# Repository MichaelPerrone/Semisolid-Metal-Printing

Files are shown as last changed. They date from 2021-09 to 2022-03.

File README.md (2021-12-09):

# Semisolid-Metal-Printing
Extrusion system for printing metal on RepRap 3D printers.

This repository contains 3D models, firmware and software configurations for installing a semisolid metal extruder on the venerable old Prusa Mendel i2 because it is a reasonably good prototyping platform. 

Eventually it will contain the same for other common RepRaps that are more popular nowadays, perhaps to be used to make pull requests for those other projects.

See the instructions on my Hackaday page:
https://hackaday.io/project/179846-semisolid-metal-printing
they are reasonably good at this point.

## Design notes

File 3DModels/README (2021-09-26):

V1 was an attempt at using MHD extrusion of liquid metal; perhaps the parts and methods used will help someone else with their project, but it didn't end up being useful for this one. Will elaborate on that system later.
V2 is the current working system. It uses a liquid gasket to enable filament extrusion of metal in just the same way as plastic.
V2 is meant to reuse some of the parts from V1, for hooking up the system to a Prusa Mendel printer. Systems for attaching to more modern printers will come after the concept has been proven out.

The V2 parts are compatible with the parts from V1 for hooking this system up to a Prusa Mendel printer and a Bondtech extruder, The spacer with all the hexagonal cuts is meant to be laser cut out of wood.
In Lieu of instructions for now, a picture of the Onshape assembly will suffice for assembly. More detailed instructions on the way.

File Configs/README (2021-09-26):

Firmware and software configs for Marlin and other 3D printing firmwares will go here.
Recommended print settings for path planning will also go here.

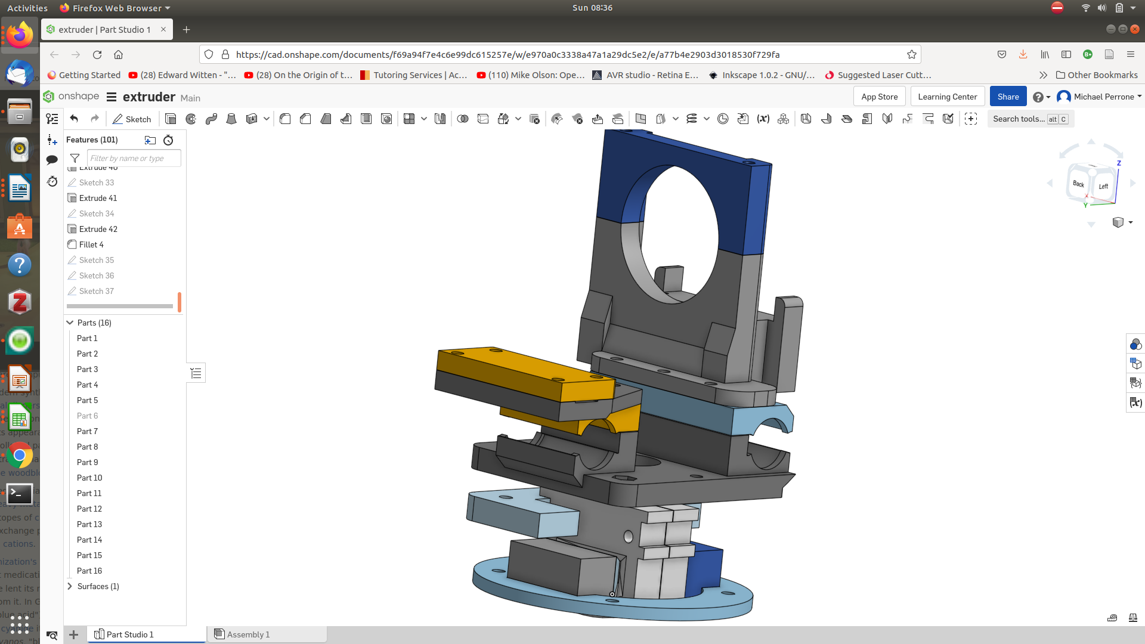
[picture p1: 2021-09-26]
3DModels/V1PrusaMendel/Screenshot from 2021-09-26 08-36-41.png

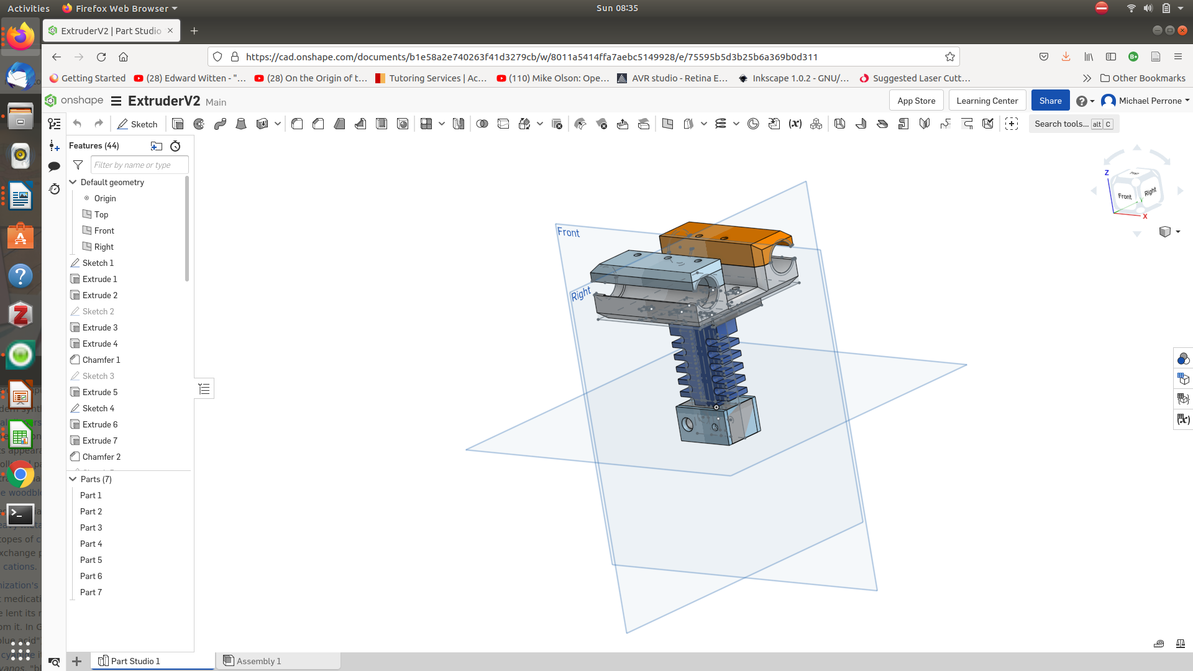
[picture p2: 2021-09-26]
3DModels/V2PrusaMendel/Screenshot from 2021-09-26 08-35-54.png

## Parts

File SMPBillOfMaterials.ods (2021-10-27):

For the extruder retrofit specifically
Item | Price | Quantity | Total | Link | Notes
M3 bolts | 11.33 | 1 | 11.33 | https://www.mcmaster.com/91290A124/
M3 bolts | 13.05 | 1 | 13.05 | https://www.mcmaster.com/91290A119/
M3 nuts | 1.17 | 1 | 1.17 | https://www.mcmaster.com/90592A085/
Mild steel bar | 9.77 | 1 | 9.77 | https://www.mcmaster.com/8910K758-9143K521/
Aluminum 6061 bar | 7.61 | 1 | 7.61 | https://www.mcmaster.com/8975K43-9140T124/ | Can cut sections of this to make thermal breaks
M6 Threaded rod | 7.5 | 1 | 7.5 | https://www.mcmaster.com/93325A418/
X-Pando | 16.91 | 1 | 16.91 | https://www.mcmaster.com/6818K11/
E3D-sized 60W heater cartridge | 8.45 | 1 | 8.45 | https://www.amazon.com/24V-60W-Temperature-Cartridge-Extruder/dp/B08CNCHC29?qsid=132-1475246-8798325
E3D Thermistor cartridge | 9.48 | 1 | 9.48 | https://www.amazon.com/Genuine-E3D-Thermistor-Cartridge-E-SEMITEC-50-MOLEX/dp/B072HNL9MR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
PETG | 21.99 | 1 | 21.99 | https://www.amazon.com/OVERTURE-Filament-Consumables-Dimensional-Accuracy/dp/B07PDV9RC8
M3 Bolts | 11.71 | 1 | 11.71 | https://www.mcmaster.com/91290A135/ | 35mm long
 |  |  | 0
 |  |  | 0
 |  |  | 0
 |  |  | 118.97 |  | Many of the components are sold in large quantities: cost can be reduced if done as a group order
For the high temperature heat bed
Item | Price | Quantity | Total | Link | Notes
Aluminum plate | 19.69 | 1 | 19.69 | https://www.mcmaster.com/9246K11/
SmCo Magnets | 4.55 | 6 | 27.3 | https://www.mcmaster.com/5716K73/
Spring Steel Sheet | 25.66 | 1 | 25.66 | https://www.mcmaster.com/9071K74/
Silicone Washers | 10.97 | 1 | 10.97 | https://www.mcmaster.com/1182N006/
High Temperature Heat Bed | 109.99 | 1 | 109.99 | https://www.filastruder.com/products/e3d-high-temperature-heated-beds
Thermal paste | 6.9 | 1 | 6.9 | https://www.amazon.com/Arctic-Silver-AS5-3-5G-Thermal-Paste/dp/B0087X728K?qsid=132-1475246-8798325
Plywood |  |  | 0 |  | tbd
M3 screws |  |  | 0 |  | tbd
m3 nuts |  |  | 0 |  | tbd
 |  |  | 0
 |  |  | 0
 |  |  | 0
 |  |  | 0
 |  |  | 0
 |  |  | 200.51 |  | Might not be 100% required to get semisolid metal printing capability, but does make it way easier
Consumables
Item | Price | Quantity | Total | Link | Notes
Borax | 13.99 | 1 | 13.99 | https://www.amazon.com/Pure-Organic-Ingredients-Multipurpose-Ingredient/dp/B01N6LF59Y
Boric acid | 6.9 | 1 | 6.9 | https://www.amazon.com/Boric-Granular-Powder-Create-solution/dp/B014JJ9846?qsid=132-1475246-8798325 | Good to stock up on borax or boric acid for when they figure out P-B11 fusion
Glycerol | 6.99 | 1 | 6.99 | https://www.amazon.com/Glycerin-Supplier-Vegetable-USP-250ml/dp/B0762179GF?qsid=132-1475246-8798325
Pentaerythritol59.99 | 59.99 | 1 | 59.99 | https://www.amazon.com/EASTCHEM-Pentaerythritol-1pound-MF-115-77-5/dp/B07QYZP89H?qsid=132-1475246-8798325
Zinc | 13.89 | 1 | 13.89 | https://www.rotometals.com/zinc-ingot-99-8-full-ingot/
Tin | 28.99 | 1 | 28.99 | https://www.rotometals.com/tin-ingot-99-9-pure/
sodium hydroxide | 13.09 | 1 | 13.09 | https://www.amazon.com/Lab-Grade-Sodium-Hydroxide-Pellet-100g/dp/B077T7K9V2
sodium or potassium nitrate | 19.95 | 1 | 19.95 | https://www.amazon.com/Potassium-Nitrate-Purity-Milled-Reagent/dp/B094JZSN51?qsid=132-1475246-8798325
sulfuric acid | 17.99 | 1 | 17.99 | https://www.amazon.com/Sulfuric-Acid-Solution-1-0M-500mL/dp/B07JBNJL3L
trisodium phosphate | 15.95 | 1 | 15.95 | https://www.amazon.com/Trisodium-Phosphate-Heavy-duty-Degreaser/dp/B098PGM45Y | Mainly for degreasing
 |  |  | 0
 |  |  | 0
 |  |  | 0
 |  |  | 0
 |  |  | 197.73 |  | Only small amounts of these are needed: can split the cost in a group order
Equipment | (For making your own filament) |  | Notes | $
Wire drawing die |  | https://www.amazon.com/NEWTRY-0-26-4-0mm-Stainless-Drawplate-Tungsten/dp/B079BGBG1H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 |  | ~50
Wire rolling mill |  | https://www.amazon.com/Jewelry-Rolling-Machine-Combination-Flatten/dp/B09HC2FTHY |  | ~250
Melting furnace |  | https://www.amazon.com/TOAUTO-Upgraded-Electric-Refining-Precious/dp/B088B8PZVK?qsid=132-1475246-8798325 | Comes with tongs and equipment | ~350
Strip casting mold |  | https://www.amazon.com/Ingot-Combination-Cavity-Wires-Double/dp/B08DDF5M55?qsid=132-1475246-8798325 |  | ~50 | These aren’t the only equipment options to do this with

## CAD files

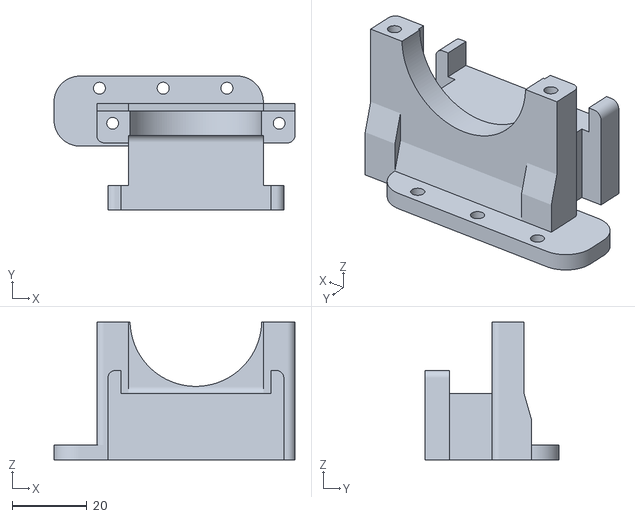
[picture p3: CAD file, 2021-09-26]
3DModels/V1PrusaMendel/Part Studio 1 - Part 10 - V1V2.stl
64.7 x 35.9 x 37.0

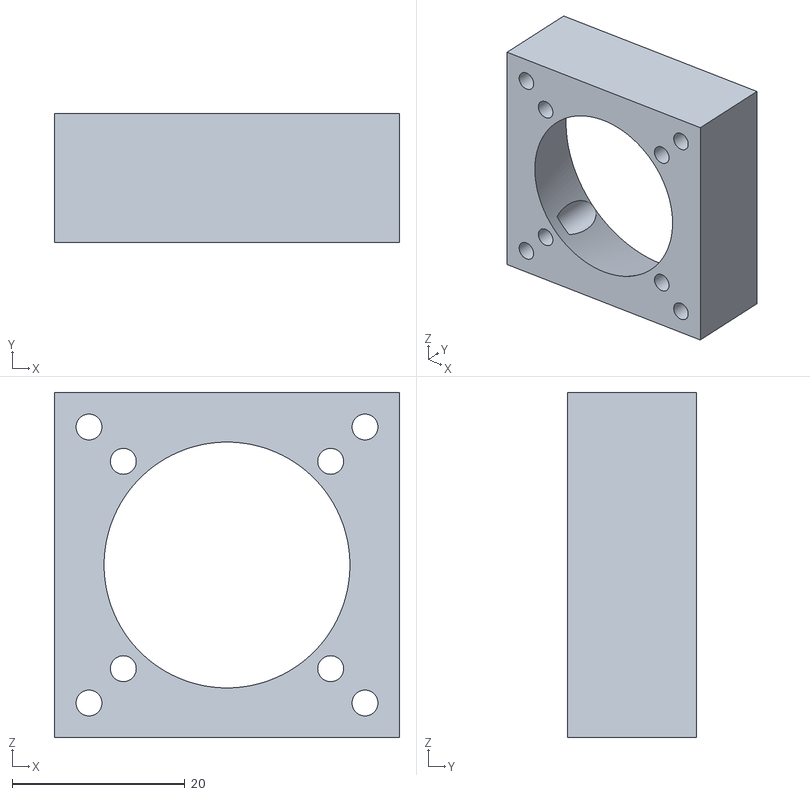
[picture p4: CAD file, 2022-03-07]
3DModels/V2PrusaMendel/Part Studio 1 - Part 22.stl
40.0 x 15.0 x 40.0

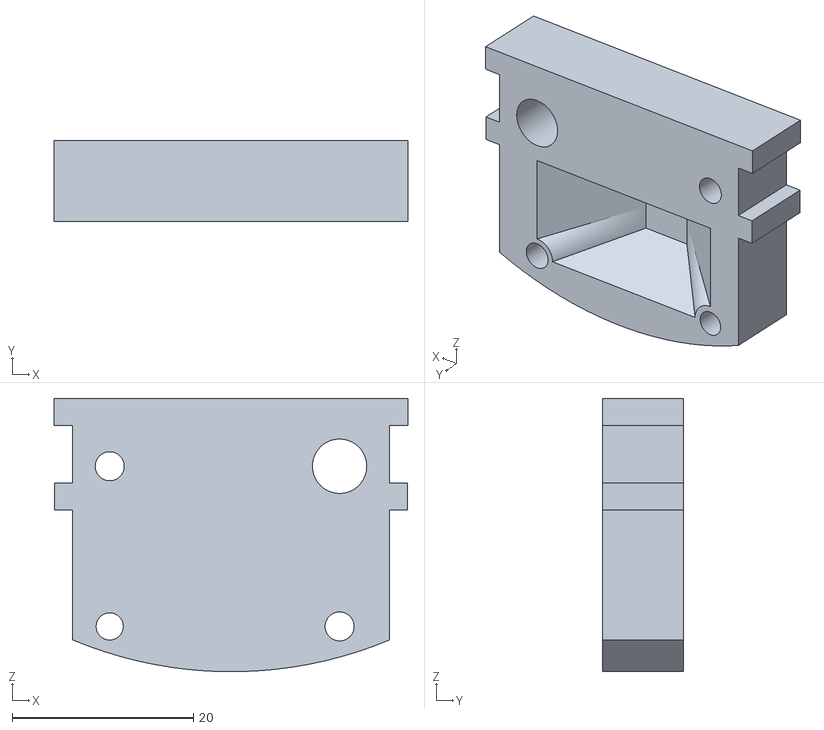
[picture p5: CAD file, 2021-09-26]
3DModels/V1PrusaMendel/Part Studio 1 - Part 13 - V1.stl
39.1 x 9.00 x 30.2

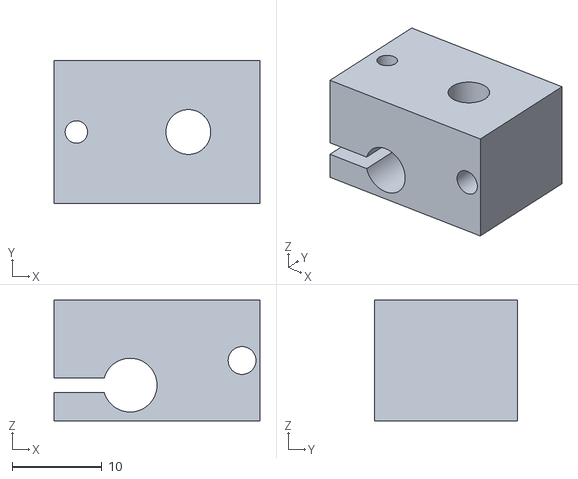
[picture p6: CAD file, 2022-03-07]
3DModels/V2PrusaMendel/Part Studio 1 - Part 23.stl
23.0 x 16.0 x 13.5

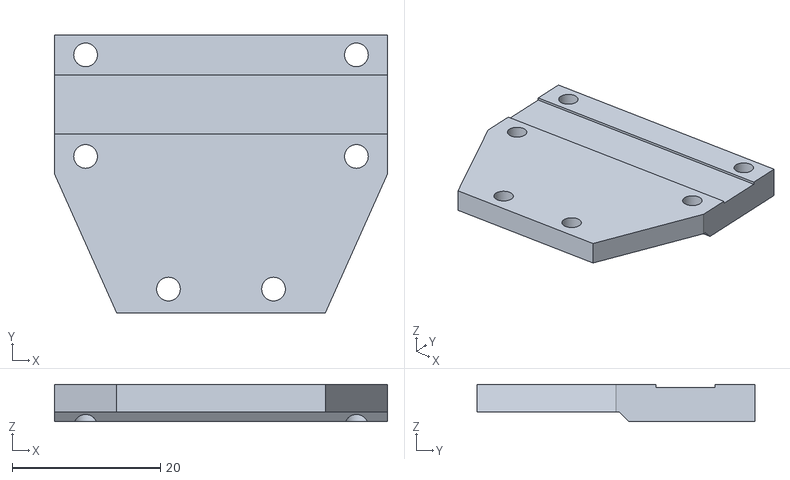
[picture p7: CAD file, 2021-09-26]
3DModels/V1PrusaMendel/Part Studio 1 - Part 15 - V1V2.stl
45.0 x 37.6 x 5.00

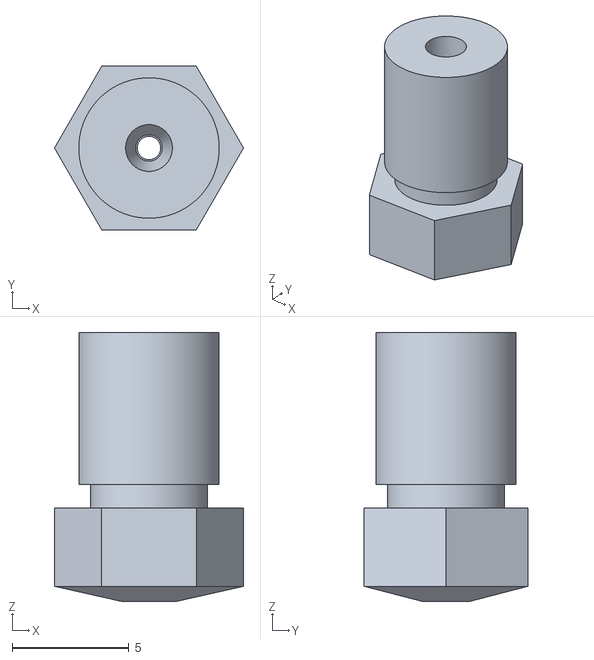
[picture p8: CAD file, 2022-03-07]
3DModels/V2PrusaMendel/Part Studio 1 - Part 25.stl
8.08 x 7.00 x 11.5

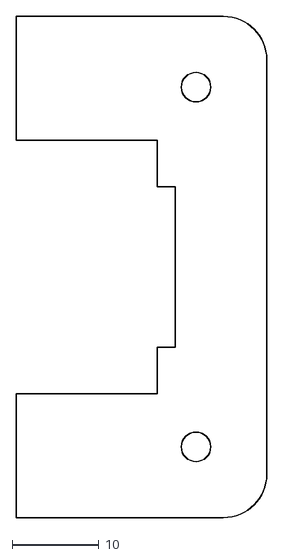
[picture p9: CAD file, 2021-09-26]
3DModels/V1PrusaMendel/Part Studio 1 - Part 14 - V1Wood.dxf
28.8 x 57.7

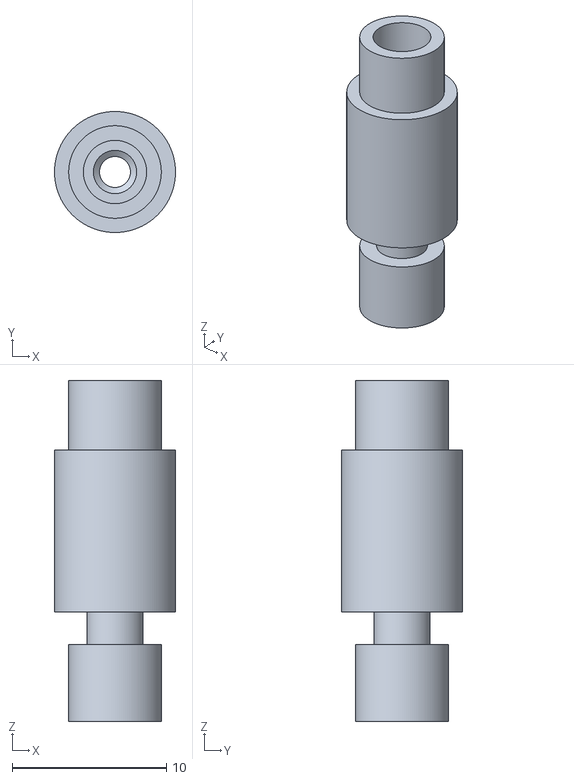
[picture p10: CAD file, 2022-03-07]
3DModels/V2PrusaMendel/Part Studio 1 - Part 24.stl
7.84 x 7.84 x 22.1

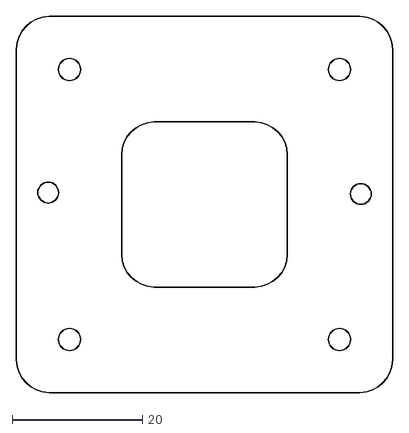
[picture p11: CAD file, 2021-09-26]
3DModels/V1PrusaMendel/Part Studio 1 - Part 6 - V1Wood.dxf
57.7 x 57.6

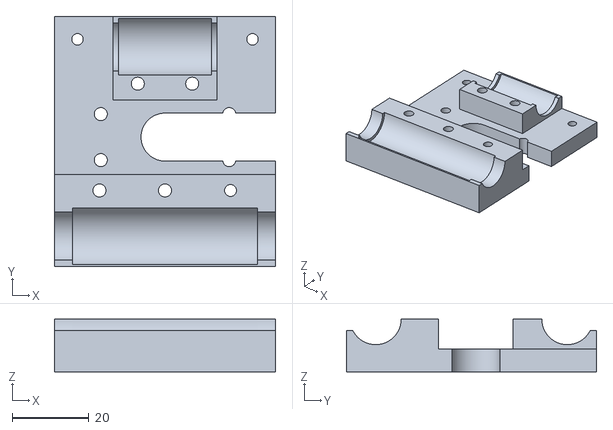
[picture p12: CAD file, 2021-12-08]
3DModels/V2PrusaMendel/Part Studio 1 - Part 13.stl
57.7 x 65.3 x 13.7

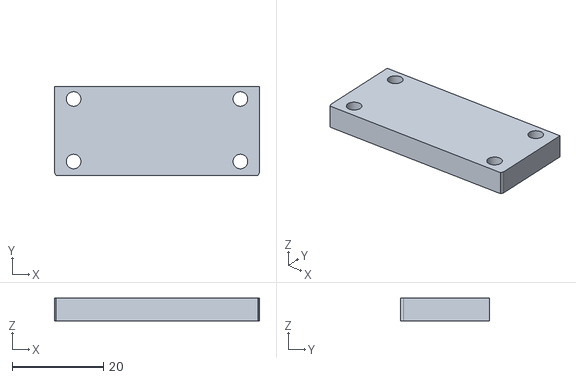
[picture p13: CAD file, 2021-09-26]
3DModels/V1PrusaMendel/Part Studio 1 - Part 16 - V1V2.stl
45.0 x 19.5 x 5.00

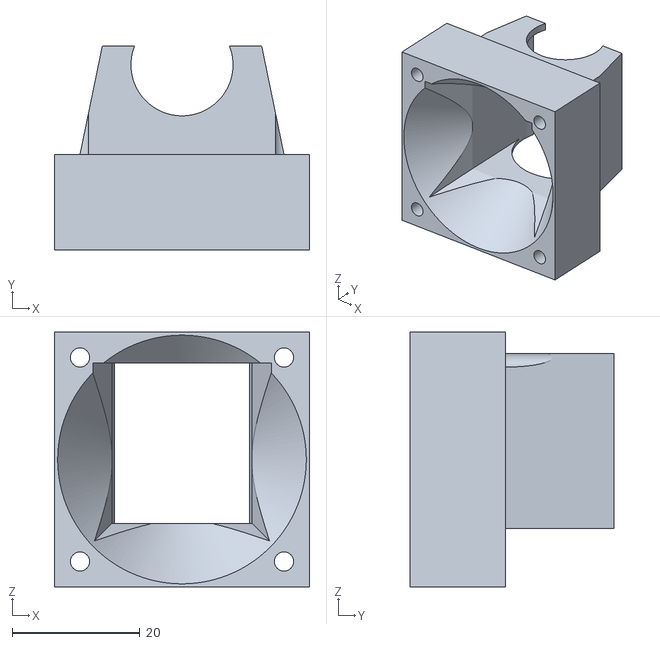
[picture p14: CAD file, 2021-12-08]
3DModels/V2PrusaMendel/Part Studio 1 - Part 19(3).stl
40.0 x 32.0 x 40.0

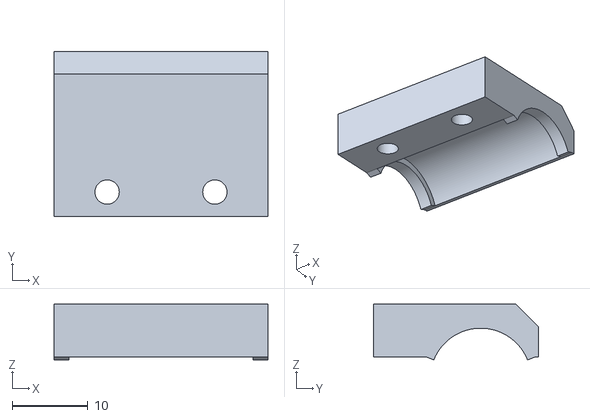
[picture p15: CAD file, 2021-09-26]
3DModels/V1PrusaMendel/Part Studio 1 - Part 8 - V1.stl
28.2 x 21.8 x 7.37

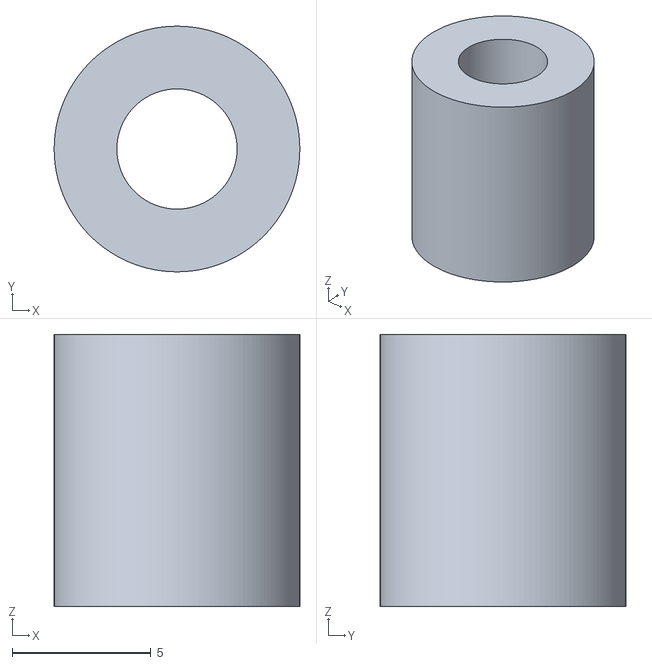
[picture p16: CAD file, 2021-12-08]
3DModels/V2PrusaMendel/Part Studio 1 - Part 21.stl
8.85 x 8.85 x 9.80

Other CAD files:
3DModels/V1PrusaMendel/Part Studio 1 - Part 12 - V1.stl
3DModels/V2PrusaMendel/Part Studio 1 - Part 14.stl
3DModels/V1PrusaMendel/Part Studio 1 - Part 6 - V1.stl
3DModels/V2PrusaMendel/Part Studio 1 - Part 20.stl
3DModels/V1PrusaMendel/Part Studio 1 - Part 1 - V1.stl
3DModels/V1PrusaMendel/Part Studio 1 - Part 1 - V1Metal.dxf
3DModels/V1PrusaMendel/Part Studio 1 - Part 11 - V1V2.stl
3DModels/V1PrusaMendel/Part Studio 1 - Part 14 - V1.stl
3DModels/V1PrusaMendel/Part Studio 1 - Part 4 - V1.stl
3DModels/V1PrusaMendel/Part Studio 1 - Part 7 - V1.stl
3DModels/V1PrusaMendel/Part Studio 1 - Part 9 - V1.stl
3DModels/V2PrusaMendel/Part Studio 1 - Part 1 - V2.stl
3DModels/V2PrusaMendel/Part Studio 1 - Part 10(1).stl
3DModels/V2PrusaMendel/Part Studio 1 - Part 16.stl
3DModels/V2PrusaMendel/Part Studio 1 - Part 17.stl
3DModels/V2PrusaMendel/Part Studio 1 - Part 2 - V2.stl
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

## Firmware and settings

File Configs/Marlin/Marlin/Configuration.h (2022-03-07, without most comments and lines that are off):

#define CONFIGURATION_H
#define CONFIGURATION_H_VERSION 010109
#define STRING_CONFIG_H_AUTHOR "(none, default config)" // Who made the changes.
#define SHOW_BOOTSCREEN
#define STRING_SPLASH_LINE1 SHORT_BUILD_VERSION // will be shown during bootup in line 1
#define STRING_SPLASH_LINE2 WEBSITE_URL         // will be shown during bootup in line 2
#define SERIAL_PORT 0
#define BAUDRATE 250000
  #define MOTHERBOARD BOARD_RAMBO
#define EXTRUDERS 1
#define DEFAULT_NOMINAL_FILAMENT_DIA 1.75
#define POWER_SUPPLY 0
#define TEMP_SENSOR_0 20
#define TEMP_SENSOR_1 0
#define TEMP_SENSOR_2 0
#define TEMP_SENSOR_3 0
#define TEMP_SENSOR_4 0
#define TEMP_SENSOR_BED 5
#define TEMP_SENSOR_CHAMBER 0
#define DUMMY_THERMISTOR_998_VALUE 25
#define DUMMY_THERMISTOR_999_VALUE 100
#define MAX_REDUNDANT_TEMP_SENSOR_DIFF 10
#define TEMP_RESIDENCY_TIME 10  // (seconds)
#define TEMP_HYSTERESIS 3       // (degC) range of +/- temperatures considered "close" to the target one
#define TEMP_WINDOW     1       // (degC) Window around target to start the residency timer x degC early.
#define TEMP_BED_RESIDENCY_TIME 10  // (seconds)
#define TEMP_BED_HYSTERESIS 3       // (degC) range of +/- temperatures considered "close" to the target one
#define TEMP_BED_WINDOW     1       // (degC) Window around target to start the residency timer x degC early.
#define HEATER_0_MINTEMP 5
#define HEATER_1_MINTEMP 5
#define HEATER_2_MINTEMP 5
#define HEATER_3_MINTEMP 5
#define HEATER_4_MINTEMP 5
#define BED_MINTEMP 5
#define HEATER_0_MAXTEMP 500
#define HEATER_1_MAXTEMP 500
#define HEATER_2_MAXTEMP 500
#define HEATER_3_MAXTEMP 500
#define HEATER_4_MAXTEMP 500
#define BED_MAXTEMP 230
#define PIDTEMP
#define BANG_MAX 255     // Limits current to nozzle while in bang-bang mode; 255=full current
#define PID_MAX BANG_MAX // Limits current to nozzle while PID is active (see PID_FUNCTIONAL_RANGE below); 255=full current
#define PID_K1 0.95      // Smoothing factor within any PID loop
  #define PID_FUNCTIONAL_RANGE 10 // If the temperature difference between the target temperature and the actual temperature
  #define DEFAULT_Kp 22.92
  #define DEFAULT_Ki 2.19
  #define DEFAULT_Kd 60.08
#define MAX_BED_POWER 255 // limits duty cycle to bed; 255=full current
#define PREVENT_COLD_EXTRUSION
#define EXTRUDE_MINTEMP 225
#define PREVENT_LENGTHY_EXTRUDE
#define EXTRUDE_MAXLENGTH 200
#define THERMAL_PROTECTION_HOTENDS // Enable thermal protection for all extruders
#define THERMAL_PROTECTION_BED     // Enable thermal protection for the heated bed
#define USE_XMIN_PLUG
#define USE_ZMIN_PLUG
#define USE_YMAX_PLUG
#define ENDSTOPPULLUPS
#define X_MIN_ENDSTOP_INVERTING false // set to true to invert the logic of the endstop.
#define Y_MIN_ENDSTOP_INVERTING false // set to true to invert the logic of the endstop.
#define Z_MIN_ENDSTOP_INVERTING false // set to true to invert the logic of the endstop.
#define X_MAX_ENDSTOP_INVERTING false // set to true to invert the logic of the endstop.
#define Y_MAX_ENDSTOP_INVERTING false // set to true to invert the logic of the endstop.
#define Z_MAX_ENDSTOP_INVERTING false // set to true to invert the logic of the endstop.
#define Z_MIN_PROBE_ENDSTOP_INVERTING false // set to true to invert the logic of the probe.
#define DEFAULT_AXIS_STEPS_PER_UNIT   { 160, 160, 2532, 500 }
#define DEFAULT_MAX_FEEDRATE          { 250, 250, 5, 25 }
#define DEFAULT_MAX_ACCELERATION      { 3000, 3000, 7, 10000 }
#define DEFAULT_ACCELERATION          3000    // X, Y, Z and E acceleration for printing moves
#define DEFAULT_RETRACT_ACCELERATION  3000    // E acceleration for retracts
#define DEFAULT_TRAVEL_ACCELERATION   3000    // X, Y, Z acceleration for travel (non printing) moves
#define DEFAULT_XJERK                 10.0
#define DEFAULT_YJERK                 10.0
#define DEFAULT_ZJERK                  0.3
#define DEFAULT_EJERK                  3.5
#define Z_MIN_PROBE_USES_Z_MIN_ENDSTOP_PIN
#define X_PROBE_OFFSET_FROM_EXTRUDER 10  // X offset: -left  +right  [of the nozzle]
#define Y_PROBE_OFFSET_FROM_EXTRUDER 10  // Y offset: -front +behind [the nozzle]
#define Z_PROBE_OFFSET_FROM_EXTRUDER 0   // Z offset: -below +above  [the nozzle]
#define MIN_PROBE_EDGE 10
#define XY_PROBE_SPEED 8000
#define Z_PROBE_SPEED_FAST HOMING_FEEDRATE_Z
#define Z_PROBE_SPEED_SLOW (Z_PROBE_SPEED_FAST / 2)
#define Z_CLEARANCE_DEPLOY_PROBE   10 // Z Clearance for Deploy/Stow
#define Z_CLEARANCE_BETWEEN_PROBES  5 // Z Clearance between probe points
#define Z_CLEARANCE_MULTI_PROBE     5 // Z Clearance between multiple probes
#define Z_PROBE_LOW_POINT          -2 // Farthest distance below the trigger-point to go before stopping
#define Z_PROBE_OFFSET_RANGE_MIN -20
#define Z_PROBE_OFFSET_RANGE_MAX 20
#define X_ENABLE_ON 0
#define Y_ENABLE_ON 0
#define Z_ENABLE_ON 0
#define E_ENABLE_ON 0 // For all extruders
#define DISABLE_X false
#define DISABLE_Y false
#define DISABLE_Z false
#define DISABLE_E false // For all extruders
#define DISABLE_INACTIVE_EXTRUDER true // Keep only the active extruder enabled.
#define INVERT_X_DIR false
#define INVERT_Y_DIR false
#define INVERT_Z_DIR false
#define INVERT_E0_DIR false
#define INVERT_E1_DIR false
#define INVERT_E2_DIR false
#define INVERT_E3_DIR false
#define INVERT_E4_DIR false
#define X_HOME_DIR -1
#define Y_HOME_DIR 1
#define Z_HOME_DIR -1
#define X_BED_SIZE 195
#define Y_BED_SIZE 195
#define X_MIN_POS -17
#define Y_MIN_POS 0
#define Z_MIN_POS 0
#define X_MAX_POS X_BED_SIZE
#define Y_MAX_POS Y_BED_SIZE
#define Z_MAX_POS 73
#define MIN_SOFTWARE_ENDSTOPS
  #define MIN_SOFTWARE_ENDSTOP_X
  #define MIN_SOFTWARE_ENDSTOP_Y
  #define MIN_SOFTWARE_ENDSTOP_Z
#define MAX_SOFTWARE_ENDSTOPS
  #define MAX_SOFTWARE_ENDSTOP_X
  #define MAX_SOFTWARE_ENDSTOP_Y
  #define MAX_SOFTWARE_ENDSTOP_Z
#define HOMING_FEEDRATE_XY (50*60)
#define HOMING_FEEDRATE_Z  (4*60)
#define EEPROM_CHITCHAT   // Give feedback on EEPROM commands. Disable to save PROGMEM.
#define HOST_KEEPALIVE_FEATURE        // Disable this if your host doesn't like keepalive messages
#define DEFAULT_KEEPALIVE_INTERVAL 2  // Number of seconds between "busy" messages. Set with M113.
#define BUSY_WHILE_HEATING            // Some hosts require "busy" messages even during heating
#define PREHEAT_1_TEMP_HOTEND 180
#define PREHEAT_1_TEMP_BED     70
#define PREHEAT_1_FAN_SPEED     0 // Value from 0 to 255
#define PREHEAT_2_TEMP_HOTEND 240
#define PREHEAT_2_TEMP_BED    110
#define PREHEAT_2_FAN_SPEED     0 // Value from 0 to 255
#define PRINTJOB_TIMER_AUTOSTART
#define LCD_LANGUAGE en
#define DISPLAY_CHARSET_HD44780 JAPANESE
#define SOFT_PWM_SCALE 0
#define SERVO_DELAY { 300 }

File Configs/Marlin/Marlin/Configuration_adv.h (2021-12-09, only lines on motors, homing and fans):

#define E0_AUTO_FAN_PIN -1
#define E1_AUTO_FAN_PIN -1
#define E2_AUTO_FAN_PIN -1
#define E3_AUTO_FAN_PIN -1
#define E4_AUTO_FAN_PIN -1
#define CHAMBER_AUTO_FAN_PIN -1
#define X_HOME_BUMP_MM 5
#define Y_HOME_BUMP_MM 5
#define Z_HOME_BUMP_MM 2
#define HOMING_BUMP_DIVISOR { 2, 2, 4 }  // Re-Bump Speed Divisor (Divides the Homing Feedrate)
#define MICROSTEP_MODES { 16, 16, 16, 16, 16 } // [1,2,4,8,16]
#define DIGIPOT_I2C_MOTOR_CURRENTS { 1.0, 1.0, 1.0, 1.0, 1.0, 1.0, 1.0, 1.0 }  //  AZTEEG_X3_PRO

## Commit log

2021-09-26 Actual initial commit, migrating the project to Github
    [Part Studio 1 - Part 1 - V1.stl, Part Studio 1 - Part 1 - V1Metal.dxf, Part Studio 1 - Part 1 - V2.stl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]
2021-10-25 components for attaching the metal extruder to a Prusa Mendel i2 Mk2 are complete
    [Part Studio 1 - Part 10(1).stl, Part Studio 1 - Part 4 - V2.stl, Part Studio 1 - Part 4(2).stl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]
2021-10-25 Added the Marlin configuration for my printer, minus PID tuning and modifying max temperatures in the thermal safety when using high temperatures for metal printing
    [Configuration.h, Configuration_adv.h]
2021-10-26 Halfway through setting Marlin config for my printing system
    [Configuration.h, Configuration_adv.h]
2021-10-26 Made initial slicer config for metal printing, almost done with Marlin config
    [Configuration.h]
2021-10-26 Finished configuring Marlin for my printing setup
    [Configuration.h]
2021-10-27 Updated bill of materials
    [SMPBillOfMaterials.ods]
2021-12-08 Played around with Slicer and firmware settings while improving print performance, added new 3D models
    [Configuration.h, Configuration_adv.h, Part Studio 1 - Part 13.stl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]
2021-12-09 Modified Thermistor 5 table to be able to take the 104GT-2 Thermistor to its absolute limit if necesary, despite being rated only up to 300C. Seems to work fine till about 340C.
    [Configuration.h, Configuration_adv.h]
2022-03-07 Made additional parts and config modifications while testing
    [Configuration.h, Part Studio 1 - Part 22.stl, Part Studio 1 - Part 23.stl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]

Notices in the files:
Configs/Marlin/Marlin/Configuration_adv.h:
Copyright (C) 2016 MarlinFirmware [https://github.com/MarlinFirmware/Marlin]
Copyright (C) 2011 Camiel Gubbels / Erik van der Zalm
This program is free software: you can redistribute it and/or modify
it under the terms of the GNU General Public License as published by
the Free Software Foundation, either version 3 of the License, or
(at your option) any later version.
